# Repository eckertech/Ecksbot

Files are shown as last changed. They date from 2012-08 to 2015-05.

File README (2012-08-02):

The ecksbot design is a sturdier and sleeker derivative of the Prusa 2 built on EckerTech innovations and putting a little more Sells Mendel back into the mix, making it a true and evolutionary RepRap.
 
We do not claim this as our own new design but rather another small step in the evolution of the RepRap hobby printer. It is designed around the concepts and efforts of the RepRap core team and should be considered as an extension of the project.
 
We would like to thank the RepRap core team for inspiring not just us but the entire RepRap community to design, redesign, innovate and think outside the box. Without the core team none of this would be possible.
 
Keeping with RepRap tradition the ecksbot is released on the GPL license making this a true RepRap 3D printer.
 
For more information on how we improved the ecksbot design over the Prusa 2 design please visit, blog.eckertech.com

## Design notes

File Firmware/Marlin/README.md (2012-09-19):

WARNING: 
--------
THIS IS RELEASE CANDIDATE 2 FOR MARLIN 1.0.0

The configuration is now split in two files
Configuration.h for the normal settings
Configuration_adv.h for the advanced settings

Gen7T is not supported.

Quick Information
===================
This RepRap firmware is a mashup between <a href="https://github.com/kliment/Sprinter">Sprinter</a>, <a href="https://github.com/simen/grbl/tree">grbl</a> and many original parts.

Derived from Sprinter and Grbl by Erik van der Zalm.
Sprinters lead developers are Kliment and caru.
Grbls lead developer is Simen Svale Skogsrud. Sonney Jeon (Chamnit) improved some parts of grbl
A fork by bkubicek for the Ultimaker was merged, and further development was aided by him.
Some features have been added by:
Lampmaker, Bradley Feldman, and others...

Features:

*   Interrupt based movement with real linear acceleration
*   High steprate
*   Look ahead (Keep the speed high when possible. High cornering speed)
*   Interrupt based temperature protection
*   preliminary support for Matthew Roberts advance algorithm 
    For more info see: http://reprap.org/pipermail/reprap-dev/2011-May/003323.html
*   Full endstop support
*   SD Card support
*   SD Card folders (works in pronterface)
*   SD Card autostart support
*   LCD support (ideally 20x4) 
*   LCD menu system for autonomous SD card printing, controlled by an click-encoder. 
*   EEPROM storage of e.g. max-velocity, max-acceleration, and similar variables
*   many small but handy things originating from bkubicek's fork.
*   Arc support
*   Temperature oversampling
*   Dynamic Temperature setpointing aka "AutoTemp"
*   Support for QTMarlin, a very beta GUI for PID-tuning and velocity-acceleration testing. https://github.com/bkubicek/QTMarlin
*   Endstop trigger reporting to the host software.
*   Updated sdcardlib
*   Heater power reporting. Useful for PID monitoring.
*   PID tuning
*   CoreXY kinematics (www.corexy.com/theory.html)

The default baudrate is 250000. This baudrate has less jitter and hence errors than the usual 115200 baud, but is less supported by drivers and host-environments.

Differences and additions to the already good Sprinter firmware:
================================================================

*Look-ahead:*

Marlin has look-ahead. While sprinter has to break and re-accelerate at each corner, 
lookahead will only decelerate and accelerate to a velocity, 
so that the change in vectorial velocity magnitude is less than the xy_jerk_velocity.
This is only possible, if some future moves are already processed, hence the name. 
It leads to less over-deposition at corners, especially at flat angles.

*Arc support:*

Slic3r can find curves that, although broken into segments, were ment to describe an arc.
Marlin is able to print those arcs. The advantage is the firmware can choose the resolution,
and can perform the arc with nearly constant velocity, resulting in a nice finish. 
Also, less serial communication is needed.

*Temperature Oversampling:*

To reduce noise and make the PID-differential term more useful, 16 ADC conversion results are averaged.

*AutoTemp:*

If your gcode contains a wide spread of extruder velocities, or you realtime change the building speed, the temperature should be changed accordingly.
Usually, higher speed requires higher temperature.
This can now be performed by the AutoTemp function
By calling M109 S<mintemp> T<maxtemp> F<factor> you enter the autotemp mode.

You can leave it by calling M109 without any F.
If active, the maximal extruder stepper rate of all buffered moves will be calculated, and named "maxerate" [steps/sec].
The wanted temperature then will be set to t=tempmin+factor*maxerate, while being limited between tempmin and tempmax.
If the target temperature is set manually or by gcode to a value less then tempmin, it will be kept without change.
Ideally, your gcode can be completely free of temperature controls, apart from a M109 S T F in the start.gcode, and a M109 S0 in the end.gcode.

*EEPROM:*

If you know your PID values, the acceleration and max-velocities of your unique machine, you can set them, and finally store them in the EEPROM.
After each reboot, it will magically load them from EEPROM, independent what your Configuration.h says.

*LCD Menu:*

If your hardware supports it, you can build yourself a LCD-CardReader+Click+encoder combination. It will enable you to realtime tune temperatures,
accelerations, velocities, flow rates, select and print files from the SD card, preheat, disable the steppers, and do other fancy stuff.
One working hardware is documented here: http://www.thingiverse.com/thing:12663 
Also, with just a 20x4 or 16x2 display, useful data is shown.

*SD card folders:*

If you have an SD card reader attached to your controller, also folders work now. Listing the files in pronterface will show "/path/subpath/file.g".
You can write to file in a subfolder by specifying a similar text using small letters in the path.
Also, backup copies of various operating systems are hidden, as well as files not ending with ".g".

*SD card folders:*

If you place a file auto[0-9].g into the root of the sd card, it will be automatically executed if you boot the printer. The same file will be executed by selecting "Autostart" from the menu.
First *0 will be performed, than *1 and so on. That way, you can heat up or even print automatically without user interaction.

*Endstop trigger reporting:*

If an endstop is hit while moving towards the endstop, the location at which the firmware thinks that the endstop was triggered is outputed on the serial port.
This is useful, because the user gets a warning message.
However, also tools like QTMarlin can use this for finding acceptable combinations of velocity+acceleration.

*Coding paradigm:*

Not relevant from a user side, but Marlin was split into thematic junks, and has tried to partially enforced private variables.
This is intended to make it clearer, what interacts which what, and leads to a higher level of modularization.
We think that this is a useful prestep for porting this firmware to e.g. an ARM platform in the future.
A lot of RAM (with enabled LCD ~2200 bytes) was saved by storing char []="some message" in Program memory.
In the serial communication, a #define based level of abstraction was enforced, so that it is clear that
some transfer is information (usually beginning with "echo:"), an error "error:", or just normal protocol,
necessary for backwards compatibility.

*Interrupt based temperature measurements:*

An interrupt is used to manage ADC conversions, and enforce checking for critical temperatures.
This leads to less blocking in the heater management routine.

Non-standard M-Codes, different to an old version of sprinter:
==============================================================
Movement:

*   G2  - CW ARC
*   G3  - CCW ARC

General:

*   M17  - Enable/Power all stepper motors. Compatibility to ReplicatorG.
*   M18  - Disable all stepper motors; same as M84.Compatibility to ReplicatorG.
*   M30  - Print time since last M109 or SD card start to serial
*   M42  - Change pin status via gcode
*   M80  - Turn on Power Supply
*   M81  - Turn off Power Supply
*   M114 - Output current position to serial port 
*   M119 - Output Endstop status to serial port

Movement variables:

*   M202 - Set max acceleration in units/s^2 for travel moves (M202 X1000 Y1000) Unused in Marlin!!
*   M203 - Set maximum feedrate that your machine can sustain (M203 X200 Y200 Z300 E10000) in mm/sec
*   M204 - Set default acceleration: S normal moves T filament only moves (M204 S3000 T7000) im mm/sec^2  also sets minimum segment time in ms (B20000) to prevent buffer underruns and M20 minimum feedrate
*   M220 - set build speed mulitplying S:factor in percent ; aka "realtime tuneing in the gcode". So you can slow down if you have islands in one height-range, and speed up otherwise.
*   M221 - set the extrude multiplying S:factor in percent
*   M400 - Finish all buffered moves.

Temperature variables:
*   M301 - Set PID parameters P I and D
*   M302 - Allow cold extrudes
*   M303 - PID relay autotune S<temperature> sets the target temperature. (default target temperature = 150C)

Advance:

*   M200 - Set filament diameter for advance
*   M205 - advanced settings:  minimum travel speed S=while printing T=travel only,  B=minimum segment time X= maximum xy jerk, Z=maximum Z jerk

EEPROM:

*   M500 - stores paramters in EEPROM. This parameters are stored:  axis_steps_per_unit,  max_feedrate, max_acceleration  ,acceleration,retract_acceleration,
  minimumfeedrate,mintravelfeedrate,minsegmenttime,  jerk velocities, PID
*   M501 - reads parameters from EEPROM (if you need reset them after you changed them temporarily).  
*   M502 - reverts to the default "factory settings".  You still need to store them in EEPROM afterwards if you want to.
*   M503 - print the current settings (from memory not from eeprom)

MISC:

*   M240 - Trigger a camera to take a photograph
*   M999 - Restart after being stopped by error

Configuring and compilation:
============================

Install the arduino software IDE/toolset v22
   http://www.arduino.cc/en/Main/Software

For gen6 and sanguinololu the Sanguino directory in the Marlin dir needs to be copied to the arduino environment.
  copy Marlin\sanguino <arduino home>\hardware\Sanguino

Install Ultimaker's RepG 25 build
    http://software.ultimaker.com
For SD handling and as better substitute (apart from stl manipulation) download
the very nice Kliment's printrun/pronterface  https://github.com/kliment/Printrun

Copy the Ultimaker Marlin firmware
   https://github.com/ErikZalm/Marlin/tree/Marlin_v1
   (Use the download button)

Start the arduino IDE.
Select Tools -> Board -> Arduino Mega 2560    or your microcontroller
Select the correct serial port in Tools ->Serial Port
Open Marlin.pde

Click the Verify/Compile button

Click the Upload button
If all goes well the firmware is uploading

Start Ultimaker's Custom RepG 25
Make sure Show Experimental Profiles is enabled in Preferences
Select Sprinter as the Driver

Press the Connect button.

KNOWN ISSUES: RepG will display:  Unknown: marlin x.y.z

That's ok.  Enjoy Silky Smooth Printing.

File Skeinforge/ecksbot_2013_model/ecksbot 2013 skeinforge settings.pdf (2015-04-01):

New Skeinforge settings for the ecksbot 2013 model.

Start by downloading the file “ecksbot_2013_Skeinforge_Settings.zip” and extract the files into a folder, we recommend a folder on your desktop for easier access.

After you have extracted the files open the folder to access the files. Next you will need to copy the “point 275” folder into the following folder “C:\Users\<Your profile name>\.skeinforge\Profiles\extrusion\”.

Next: The alterations folder has the start and end code files that will be placed at the beginning and the end of your gcode files when they are sliced in Skeinforge. Before copying the alterations folder into .skeinforge you should open the startcode.gcode and the endcode.gcode files in a text editor i.e. Notepad and adjust the temperatures to suit your machine.

The startcode.gcode, hot end temperature is set using the M109 command to set the temperature and wait until the hot end normalizes.

The file is set to 250 degrees using M109 S250.0 ;set temperature and wait.
To change the temperature to suit your machine just change the numerals
E.g. M109 S245.0 ;set temperature and wait.
And then save the file.

(Also, Skeinforge does not have a print cooling feature. So, we have placed an M106 S127.0 code into the startup code that will set the initial speed of the print cooling fan to 50% (recommended minimum setting). This value can be changed from 0-255. Where anything under 100 seems to turn the fan off, 127 is 50% and 255 is 100% speed.)

The endcode.gcode file simply moves the hot end out of the way after the print has finished and resets the hot end and bed temperatures to start up settings. Change the M104 S250.0 to your startup hot end temperature and the M140 S105.0 to your to your startup heated bed temperature. And save the file

When both files are updated, copy the complete “alterations” folder into “C:\Users\<Your profile name>\.skeinforge\”. These folders may be a little different for you depending on your operating system. If all else fails you can use the search feature on your computer to find the correct “.skeinforge” folder.

NOTE: If you still cannot find the “.skeinforge” folder open up Repetier and click on the “Slicer” tab. Next, click on the “Activate” button in the Skeinforge panel (Repetier 0.85b) or select Skeinforge in the “Slicer” drop down menu for later versions of Repetier. Now click the configure button. This will create the initial “.skeinforge” folders. Close and reopen Repetier and go back to the “Slicer” tab. You should now see an “ABS” profile located in the “Skeinforge” profile drop down. Proceed with copying the files into the proper folders.

After you have copied the files into the proper folders open Repetier. Click on the Slicer tab and click on the “Activate” button in the Skeinforge panel (Repetier 0.85b) or select Skeinforge in the “Slicer” drop down menu for later versions of Repetier*. Next, select the point 275 in the “profile” drop down list. This will ensure that when you go to slice your next object the Skeinforge slicer will be used instead of Slic3r.

Notes:

- If the point 275 profile does not show up try closing and reopening Repetier.
- We recommend using Repetier 0.85b as it seems to slice objects faster and we have never had an issue using this version.

Before you start slicing your objects you will first need to change the temperature for the hot end and heated bed inside of Skeinforge. Click on the “Configure” button in the Skeinforge panel in Repetier. This will open up Skeinforge. Next make sure that the Profile type is set to “Extrusion” and the Profile Selection is set to “point 275”.

First let’s change the hot end temperature. Click on the “Temperature” button/tab. This will load the temperature settings for the hot end. Change every value in the “Temperature” panel to your machines extrusion temperature. It is likely close to 250.

Next, let’s change the heated bed temperatures. Click on the “Chamber” button/tab. Change the Bed Temperature (Celsius) box to your beginning heated bed temperature setting. We recommend 105 as measured with the supplied thermocouple. Now, change the Bed Temperature End (Celsius) box to the temperature you would like to increase to over the first 8mm of the print. We recommend 115 as measured with the supplied thermocouple. If you choose not to increase the heated bed temperature as the printer progresses through your prints simply set these 2 boxes to the same temperature.

Click the “Save All” button and close Skeinforge. You can now use Skeinforge to slice up and print your objects.

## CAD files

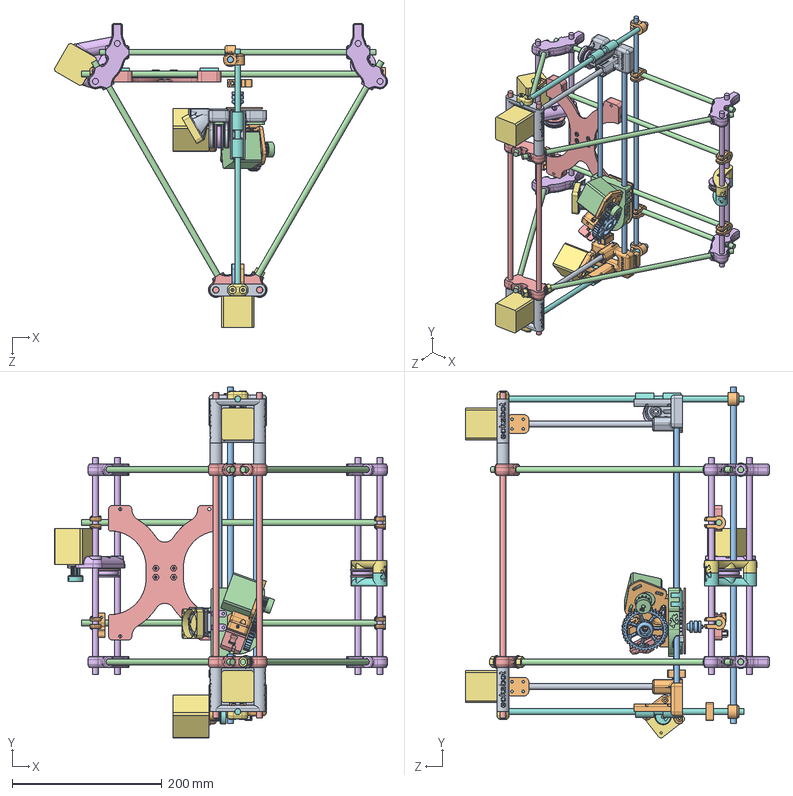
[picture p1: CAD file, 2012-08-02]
Assembly.SLDASM
445.2 x 469.2 x 407.0 mm
Ecksbot_x_end_idlerx1
Ecksbot_x_end_motorx1
X_Bearing_rodsx2 x 2
xCarriagex1
BearingHousingInnerx3 x 3
BearingHousingOuterx3 x 3
Nema17_82ozin x 4
BeltPulleyx2 x 2
z-motor-mountx2 x 2
Eckstruder-16mm-insertx1
EckstruderBigGearx1
Nema17_60ozin
Eckstruder_Idlerx1
xBeltClampx2 x 2
40mm_Fan
LinearBearing_LM8UU x 11
Fan_Cowlx1
Heatsink
BrassNozzle
Vertex_ThreadedRodx6 x 6
Top_ThreadedRodx2 x 2
Bottom_ThreadedRodx4 x 4
ZBarClampx2 x 2
Z-Bearing-rodsx2 x 2
Z-Drive-threaded-rodx2 x 2
Bar_Clampx8 x 8
Z-Holder-Threaded-Rodx1
Y-Bearing-rodsx2 x 2
Y_Cartx1
Ecksbot_Y_Motor_Mountx1
Y_Idler_Rightx1
Y_Idler_leftx1
Y_Belt_Clampx2 x 2
CouplerLeftx2 x 2
CouplerRightx2 x 2
EckstruderSmallPulley_Grubx1
Eckertech-Vertex_x2 x 2
Ecksbot_Vertex_Footedx2 x 4
8mm-Nut x 2
8mm-Washer x 2
spacerx2 x 2
Eckertech_End_Stop_Holderx3 x 3

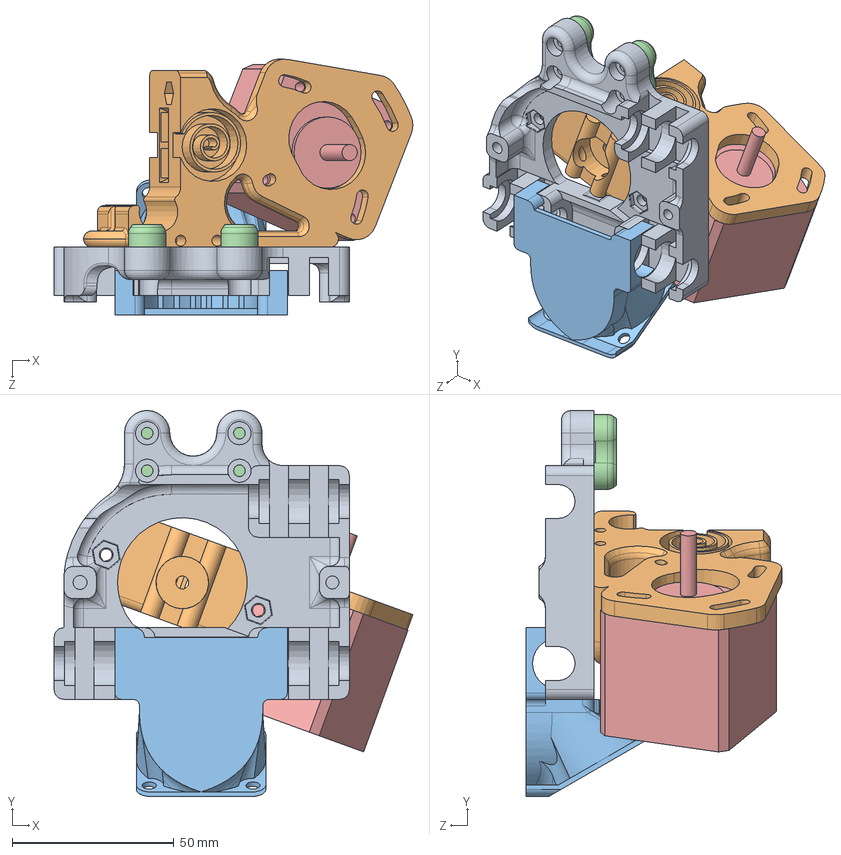
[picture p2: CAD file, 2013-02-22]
Mods/Prusa Carriage Mod/NoHookAssembly.SLDASM
110.7 x 119.2 x 78.9 mm
xCarriage_frontbelt_NoHook
Eckstruder-16mm-insert-NoHook
Fan_Cowl
BeltClamp x 2
Nema17_60ozin

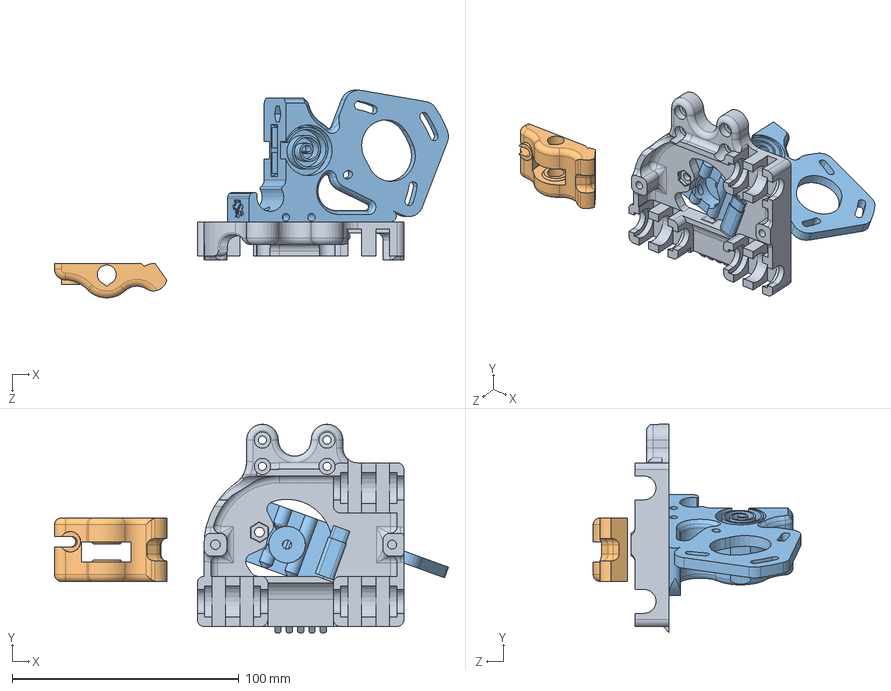
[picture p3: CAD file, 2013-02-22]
Mods/Prusa Carriage Mod/Assembly.SLDASM
173.7 x 92.0 x 91.6 mm
xCarriage_frontbelt
Eckstruder_Idler
Eckstruder-16mm-insertx1

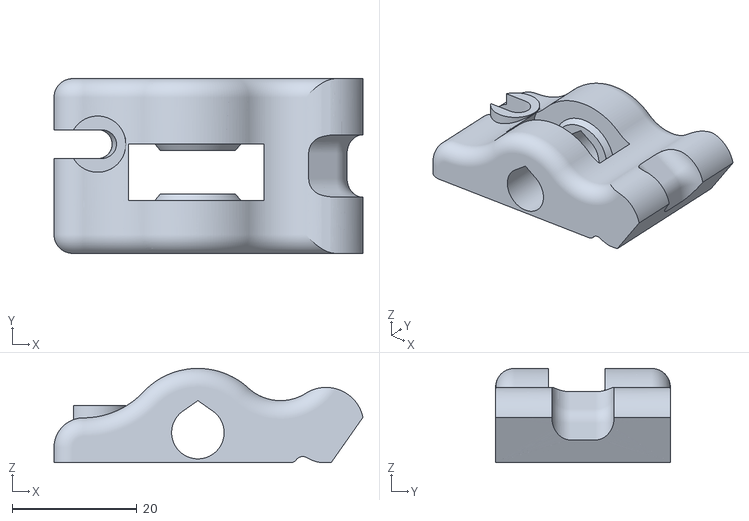
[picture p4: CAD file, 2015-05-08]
ecksbot_model_2014/STLs/Gears_Pulleys_Idler/Eckstruder_Idler_1.STL
49.5 x 28.0 x 15.1

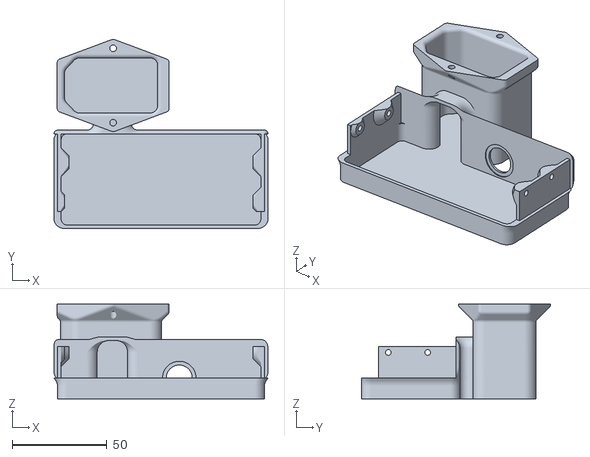
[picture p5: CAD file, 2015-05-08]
ecksbot_model_2014/STLs/PSU_Cover/PSU_Cover.STL
112.9 x 99.9 x 50.0

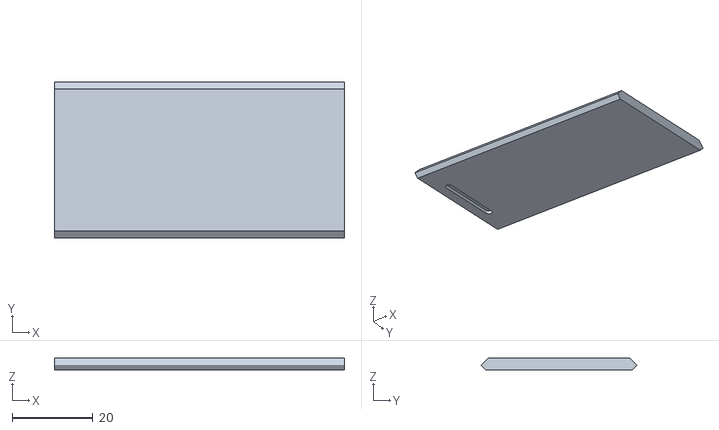
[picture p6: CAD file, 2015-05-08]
ecksbot_model_2014/STLs/RAMPS_Case/RAMPs_PanelCover_withdisplay_1.STL
72.0 x 38.8 x 3.00

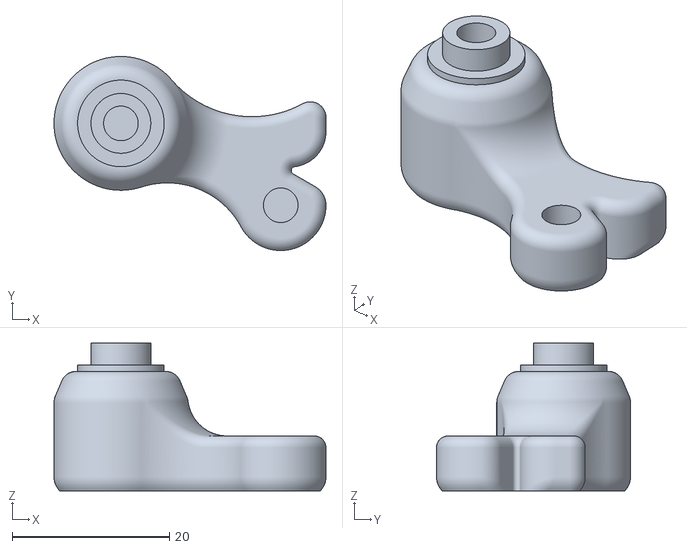
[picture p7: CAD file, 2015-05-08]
ecksbot_model_2014/STLs/Tray4/y_idler_tensioner_right_1.STL
34.6 x 24.7 x 18.8

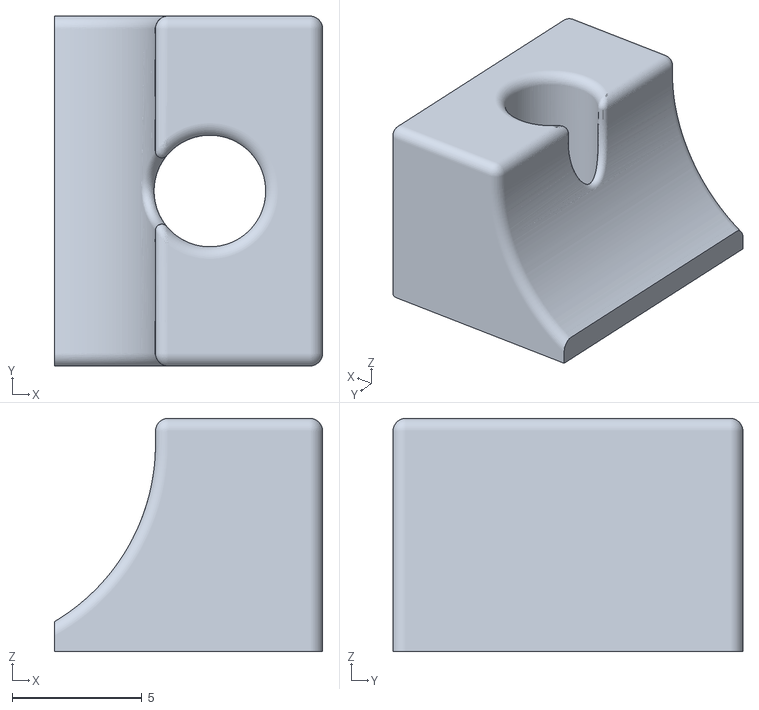
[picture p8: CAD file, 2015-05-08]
ecksbot_model_2014/STLs/Tray5/y_carriage_bearing_clamp_4.STL
10.3 x 13.5 x 9.00

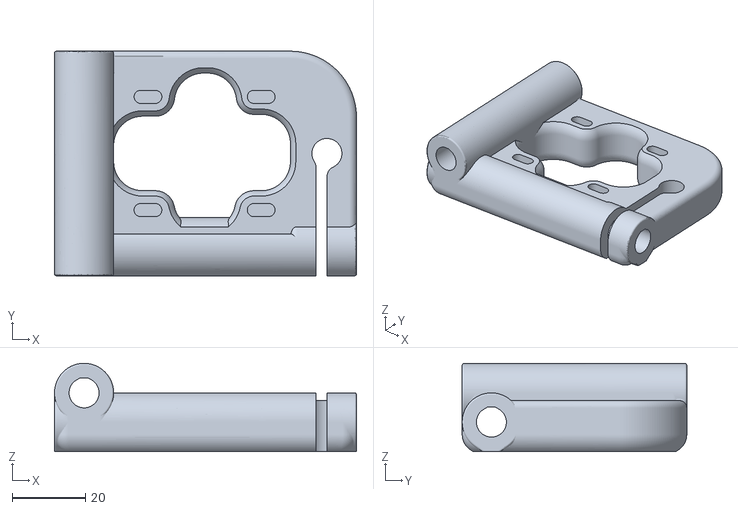
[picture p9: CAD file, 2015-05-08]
ecksbot_model_2014/STLs/Tray6/z_motor_holder_2_1.STL
82.7 x 61.5 x 24.2

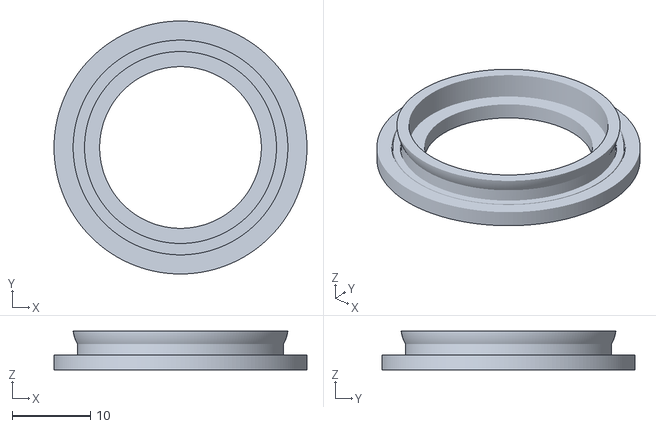
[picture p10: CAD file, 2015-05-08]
ecksbot_model_2014/STLs/Tray7/y_idler_top_4.STL
32.3 x 32.3 x 4.95

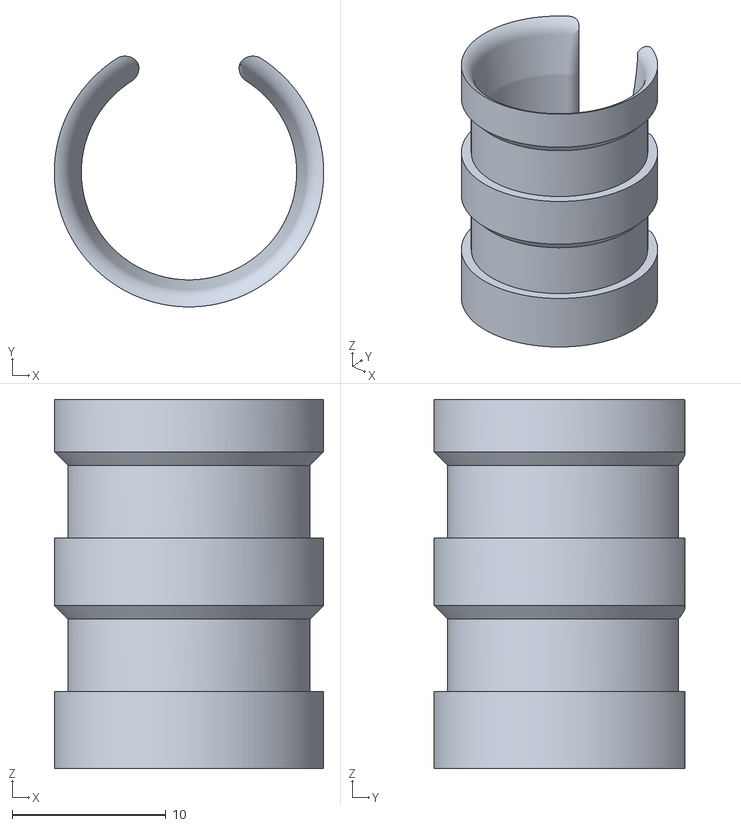
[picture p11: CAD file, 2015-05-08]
ecksbot_model_2014/STLs/Tray8/spiral_wrap_collar1_2.STL
17.5 x 16.3 x 24.0

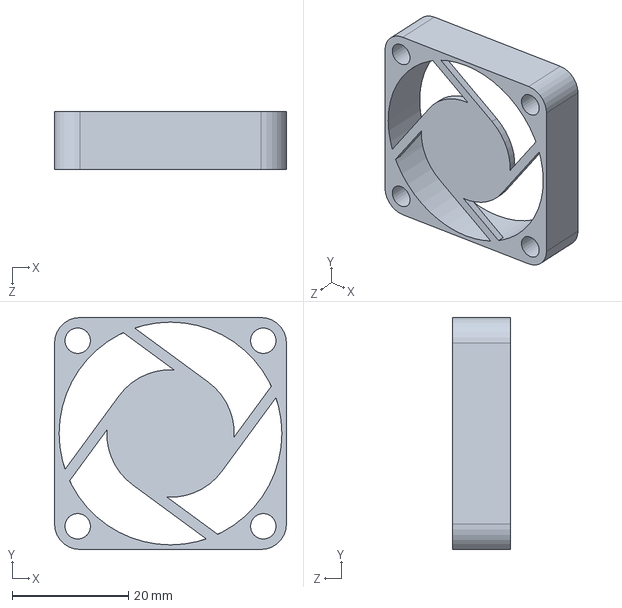
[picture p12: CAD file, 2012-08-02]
Mechanical Parts/40mm_Fan.SLDPRT
40.0 x 40.0 x 10.0 mm

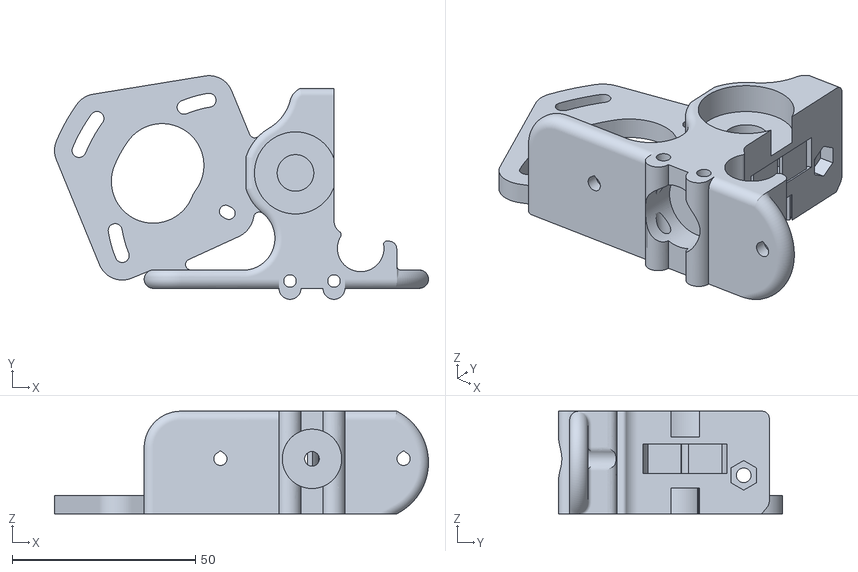
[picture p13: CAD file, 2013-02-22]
Mods/Prusa Carriage Mod/STLs/No Hook/Eckstruder-16mm-insert-NoHook.STL
102.1 x 61.0 x 28.0

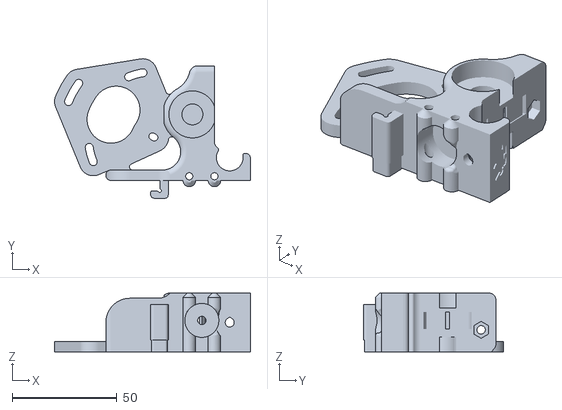
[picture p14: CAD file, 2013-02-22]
Mods/Prusa Carriage Mod/STLs/With Hook/Eckstruder-16mm-insertx1.STL
93.5 x 66.5 x 28.0

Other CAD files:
Mods/Prusa Carriage Mod/Eckstruder_Idler.SLDPRT
Mods/Spiral Wrap/PSU_Cover.SLDPRT
Plastic Parts/Solidworks/z-motor-mountx2.SLDPRT
Plastic Parts/Step/Eckertech_End_Stop_Holderx3.STEP
Mechanical Parts/8mm-Nut.SLDPRT
Mechanical Parts/8mm-Washer.SLDPRT
Mechanical Parts/Bottom_ThreadedRodx4.SLDPRT
Mechanical Parts/BrassNozzle.SLDPRT
Mechanical Parts/Heatsink.SLDPRT
Mechanical Parts/LinearBearing_LM8UU.SLDPRT
Mechanical Parts/Nema17_60ozin.SLDPRT
Mechanical Parts/Nema17_82ozin.SLDPRT
Mechanical Parts/Top_ThreadedRodx2.SLDPRT
Mechanical Parts/Vertex_ThreadedRodx6.SLDPRT
Mechanical Parts/X_Bearing_rodsx2.SLDPRT
Mechanical Parts/Y-Bearing-rodsx2.SLDPRT
Mechanical Parts/Z-Bearing-rodsx2.SLDPRT
Mechanical Parts/Z-Drive-threaded-rodx2.SLDPRT
Mechanical Parts/Z-Holder-Threaded-Rodx1.SLDPRT
Mechanical Parts/microswitch.SLDPRT
Mods/Prusa Carriage Mod/BeltClamp.SLDPRT
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

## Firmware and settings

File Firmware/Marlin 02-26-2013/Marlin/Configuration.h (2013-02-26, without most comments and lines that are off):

#define CONFIGURATION_H
#define STRING_VERSION_CONFIG_H "2012-05-02" //Personal revision number for changes to THIS file.
#define STRING_CONFIG_H_AUTHOR "erik" //Who made the changes.
#define BAUDRATE 250000
#define MOTHERBOARD 33
#define TEMP_SENSOR_0 1
#define TEMP_SENSOR_1 0
#define TEMP_SENSOR_2 0
#define TEMP_SENSOR_BED 4
#define TEMP_RESIDENCY_TIME 10	// (seconds)
#define TEMP_HYSTERESIS 3       // (degC) range of +/- temperatures considered "close" to the target one
#define TEMP_WINDOW     1       // (degC) Window around target to start the recidency timer x degC early.
#define HEATER_0_MINTEMP 5
#define HEATER_1_MINTEMP 5
#define HEATER_2_MINTEMP 5
#define BED_MINTEMP 5
#define HEATER_0_MAXTEMP 330
#define HEATER_1_MAXTEMP 275
#define HEATER_2_MAXTEMP 275
#define BED_MAXTEMP 150
#define PID_MAX 255 // limits current to nozzle; 255=full current
#define PREVENT_DANGEROUS_EXTRUDE
#define PREVENT_LENGTHY_EXTRUDE
#define EXTRUDE_MINTEMP 170
#define EXTRUDE_MAXLENGTH (X_MAX_LENGTH+Y_MAX_LENGTH) //prevent extrusion of very large distances.
#define ENDSTOPPULLUPS // Comment this out (using // at the start of the line) to disable the endstop pullup resistors
  #define ENDSTOPPULLUP_XMAX
  #define ENDSTOPPULLUP_YMAX
  #define ENDSTOPPULLUP_ZMAX
  #define ENDSTOPPULLUP_XMIN
  #define ENDSTOPPULLUP_YMIN
  #define ENDSTOPPULLUP_ZMIN
const bool X_ENDSTOPS_INVERTING = false; // set to true to invert the logic of the endstops.
const bool Y_ENDSTOPS_INVERTING = false; // set to true to invert the logic of the endstops.
const bool Z_ENDSTOPS_INVERTING = false; // set to true to invert the logic of the endstops.
#define X_ENABLE_ON 0
#define Y_ENABLE_ON 0
#define Z_ENABLE_ON 0
#define E_ENABLE_ON 0 // For all extruders
#define DISABLE_X false
#define DISABLE_Y false
#define DISABLE_Z false
#define DISABLE_E false // For all extruders
#define INVERT_X_DIR true    // for Mendel set to false, for Orca set to true
#define INVERT_Y_DIR false    // for Mendel set to true, for Orca set to false
#define INVERT_Z_DIR true     // for Mendel set to false, for Orca set to true
#define INVERT_E0_DIR false   // for direct drive extruder v9 set to true, for geared extruder set to false
#define INVERT_E1_DIR false    // for direct drive extruder v9 set to true, for geared extruder set to false
#define INVERT_E2_DIR false   // for direct drive extruder v9 set to true, for geared extruder set to false
#define X_HOME_DIR -1
#define Y_HOME_DIR -1
#define Z_HOME_DIR -1
#define min_software_endstops true //If true, axis won't move to coordinates less than HOME_POS.
#define max_software_endstops true  //If true, axis won't move to coordinates greater than the defined lengths below.
#define X_MAX_POS 205
#define X_MIN_POS 0
#define Y_MAX_POS 205
#define Y_MIN_POS 0
#define Z_MAX_POS 140
#define Z_MIN_POS 0
#define X_MAX_LENGTH (X_MAX_POS - X_MIN_POS)
#define Y_MAX_LENGTH (Y_MAX_POS - Y_MIN_POS)
#define Z_MAX_LENGTH (Z_MAX_POS - Z_MIN_POS)
#define X_HOME_POS 0
#define Y_HOME_POS 0
#define Z_HOME_POS 0
#define NUM_AXIS 4 // The axis order in all axis related arrays is X, Y, Z, E
#define HOMING_FEEDRATE {50*60, 50*60,3*60, 0}  // set the homing speeds (mm/min)
#define DEFAULT_AXIS_STEPS_PER_UNIT   {80,80,2560,550}  // default steps for metric ecksbot
#define DEFAULT_MAX_FEEDRATE          {500, 500, 3, 45}    // (mm/sec)
#define DEFAULT_MAX_ACCELERATION      {2800,2800,3,2800}    // X, Y, Z, E maximum start speed for accelerated moves. E default values are good for skeinforge 40+, for older versions raise them a lot.
#define DEFAULT_ACCELERATION          2000    // X, Y, Z and E max acceleration in mm/s^2 for printing moves
#define DEFAULT_RETRACT_ACCELERATION  6000   // X, Y, Z and E max acceleration in mm/s^2 for r retracts
#define DEFAULT_XYJERK                24.0    // (mm/sec)
#define DEFAULT_ZJERK                 0.2     // (mm/sec)
#define DEFAULT_EJERK                 0.5    // (mm/sec)
#define EEPROM_SETTINGS
#define EEPROM_CHITCHAT
#define SDSUPPORT // Enable SD Card Support in Hardware Console
#define FAST_PWM_FAN
#include "Configuration_adv.h"
#include "thermistortables.h"

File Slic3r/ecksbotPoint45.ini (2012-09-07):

acceleration = 0
bed_size = 200,200
bed_temperature = 101
bridge_fan_speed = 100
bridge_flow_ratio = 1
bridge_speed = 60
brim_width = 0
complete_objects = 0
cooling = 0
disable_fan_first_layers = 1
duplicate = 1
duplicate_distance = 6
duplicate_grid = 1,1
end_gcode = M104 S0 ; turn off temperature\nG28 X0  ; home X axis\nM84     ; disable motors
extra_perimeters = 1
extruder_clearance_height = 20
extruder_clearance_radius = 20
extrusion_axis = E
extrusion_multiplier = 1
extrusion_width = 0
fan_always_on = 0
fan_below_layer_time = 60
filament_diameter = 2.85
fill_angle = 45
fill_density = 0.2
fill_pattern = honeycomb
first_layer_bed_temperature = 111
first_layer_extrusion_width = 0
first_layer_height = 100%
first_layer_speed = 90%
first_layer_temperature = 220
g0 = 0
gcode_arcs = 0
gcode_comments = 0
gcode_flavor = reprap
infill_acceleration = 50
infill_every_layers = 1
infill_extrusion_width = 0
infill_speed = 60
layer_gcode = 
layer_height = 0.2
max_fan_speed = 100
min_fan_speed = 35
min_print_speed = 10
notes = 
nozzle_diameter = 0.45
output_filename_format = [input_filename_base].gcode
perimeter_acceleration = 25
perimeter_speed = 48
perimeters = 3
perimeters_extrusion_width = 0
post_process = 
print_center = 100,100
randomize_start = 1
retract_before_travel = 2
retract_length = .8
retract_lift = 0
retract_restart_extra = 0
retract_speed = 50
rotate = 0
scale = 1
skirt_distance = 6
skirt_height = 1
skirts = 1
slowdown_below_layer_time = 15
small_perimeter_speed = 48
solid_fill_pattern = rectilinear
solid_infill_speed = 60
solid_layers = 3
start_gcode = G28 ; home all axes
support_material = 0
support_material_angle = 0
support_material_pattern = rectilinear
support_material_spacing = 2.5
support_material_threshold = 45
support_material_tool = 0
temperature = 220
threads = 2
top_solid_infill_speed = 60
travel_speed = 160
use_relative_e_distances = 0
z_offset = 0

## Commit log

2012-08-02 Ecksbot Version 1.0
    [40mm_Fan.SLDPRT, 8mm-Nut.SLDPRT, 8mm-Washer.SLDPRT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]
2012-08-25 updated with hot-end and component wiring
2012-08-27 Only zip ties and spiral wrap left, all wiring complete
2012-08-30 Complete first draft of the wiring instructions
    This is the rough draft of the wiring instructions. We will be using it
    as a basis for creating the wiring forum thread on the eckertech forum.
    http://forum.eckertech.com
2012-09-07 The Ecksbot marlin firmware
    The settings in this file form a basis for operating your ecksbot. Fine
    tuning can be accomplished by changing settings in the configuration.h
    file.
2012-09-07 Ecksbot Slic3r settings - 0.2mm layer height
    These settings can be loaded into Slic3r and saved in the drop down
    menus. Our current default settings allow for very nice prints at a
    0.2mm layer height. As we fine tune the default ecksbot settings, and
    add settings for differing layer heights, we'll post the updates here.
2012-09-17 Reoriented to print on the proper flat side
    [BearingHousingInnerx3.STL, BearingHousingOuterx3.STL, CouplerLeftx2.STL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]
2012-09-17 Widened the through hole to 8.4mm
    The bar clamp was fitting a bit too snuggly (more like not fitting
    without drilling). Therefore widened the hole out to 8.4mm, which
    should fix the issue on most printers.
    [Bar_Clampx8.SLDPRT, Bar_Clampx8.STEP, Bar_Clampx8.stl]
2012-09-17 Widened bed mount holes, + replicator printable
    Widened the bed mount holes to 5.3mm to allow for small variations in
    the standoff placement on the bed itself. Also added a makerbot
    replicator printable sized carriage.
    [Y_Cart_ReplicatorResize_x1.SLDPRT, Y_Cart_ReplicatorResize_x1.STEP, Y_Cart_ReplicatorResize_x1.STL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]
2012-09-18 Changed the orientation for proper printing
    Flipped the part over so that it will print from the correct face
    [Eckertech_End_Stop_Holderx3.SLDPRT, Eckertech_End_Stop_Holderx3.STEP, Eckertech_End_Stop_Holderx3.STL]
2012-09-19 added the individual marlin files
    For those that are cloning our design using github, this is a bit easier
    a deployment.
    [Configuration.h, Configuration_adv.h]
2012-09-20 How to flash firmware onto your RAMPs using arduino
    How to flash firmware onto your RAMPs using the arduino sofware package.
2012-12-18 ecksbot skeinforge settings
    We have developed these Skeinforge settings specifically for the ecksbot
    and a 0.45mm nozzle.
2013-02-22 Prusa Carriage Mod
    This is a mod to the ecksbot X-Carriage that will allow it to be printed
    as a drop in replacement to the regular carriage found on numerous Prusa
    Mendel variants (i.e. prusa 1, prusa it2, wallace, mix G1, etc.) There
    are 2 version, one with a printed hook to further reduce hardware
    commits and one withou the hook so that different extruder blocks can be
    used.
    [Assembly.SLDASM, BeltClamp.SLDPRT, BeltClamp.STL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]
2013-02-26 Marlin Firmware with new Accel Settings
    This is the latest supported firmware with new acceleration settings for
    the Ecksbot.
    [Configuration.h, Configuration_adv.h]
2013-03-04 New settings for Slic3r 0.9.8
    Don't forget to change the temperature settings to the values for your
    ecksbot
2013-03-20 Version 1a of the Spiral Wrap Addons
    Addition of spiral wrap holders to the ecksbot to alleviate wire stress
    and clean up the design.
    [BarAdapter.SLDPRT, Eckstruder_SpiralWrap.SLDPRT, SpiralWrapCollar1.SLDPRT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]
2013-03-20 2 possible PSU covers with plug and switch holder
    I'm not happy with either design yet, but they are functional.
    [PSU_Cover.SLDPRT, PSU_Cover2.SLDPRT]
2015-05-08 ecksbot model 2014 STL files
    This contains all of the STL files required to build an ecksbot model
    2014, plus a few extras (Ramps case, PSU cover, spiral wrap connectors
    and wiring base). We have also included the trays that we use when
    printing an ecksbot 2014. All STL file names come with a trailing "_#".
    The # indicates the required quantity of that part.
    [10ToothPulley_2.STL, Eckstruder_Idler_1.STL, Eckstruder_SmallPulley_1.STL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]
